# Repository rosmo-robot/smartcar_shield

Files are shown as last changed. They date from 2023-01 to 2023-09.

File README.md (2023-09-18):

# Smartcar shield 2.0







A versatile and easy to use vehicle platform for hobby & Academic projects

## Description
This repository, includes everything necessary to set up a Smartcar 2.0. The 100% open hardware robot down to component level.

The Smartcar, is a vehicular educational platform, which enables the user to develop various robotic applications in an affordable, pedagogic and easy way. It is intended to be accessible for persons with basic programming knowledge and little to no experience of electronics. It additionally supports the needs of more experienced users.

## Smartcar 2.0 (In development)

Licence: CERN-OHL-P

 Features;
 
 * Mounting space for SBC; Beagle AI64, Play, Pi, Jetson Nano, etc 
 * Reference implimentation of Arduino / [Smartcar Library](https://github.com/rosmo-robot/smartcar_shield/blob/master/README.md
 * Reference implimentation of [ROS2/Linorobot2](https://github.com/hippo5329/linorobot2_hardware)
 * Use of 4s LifePO4 or 3s Lipo batteries
 * Dual motor drivers for 4x4 & optional [mecanum drive](https://community.robotshop.com/forum/t/nema-17-mecanum-wheels/55901)
 * [mikroBUS socket](https://www.mikroe.com/mikrobus-shuttle-127mm-2x8-pin-box-header-smd-male)
 * Expanded I2C/ SPI connectors using [Breakout Garden](https://shop.pimoroni.com/collections/breakout-garden), [Qwiic](https://soldered.com/categories/easyc-2/)

### Project Status

 * [Motor board](https://kicanvas.org/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) ordered awaiting testing
   
 * [Pico board](https://kicanvas.org/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) ordered awaiting testing

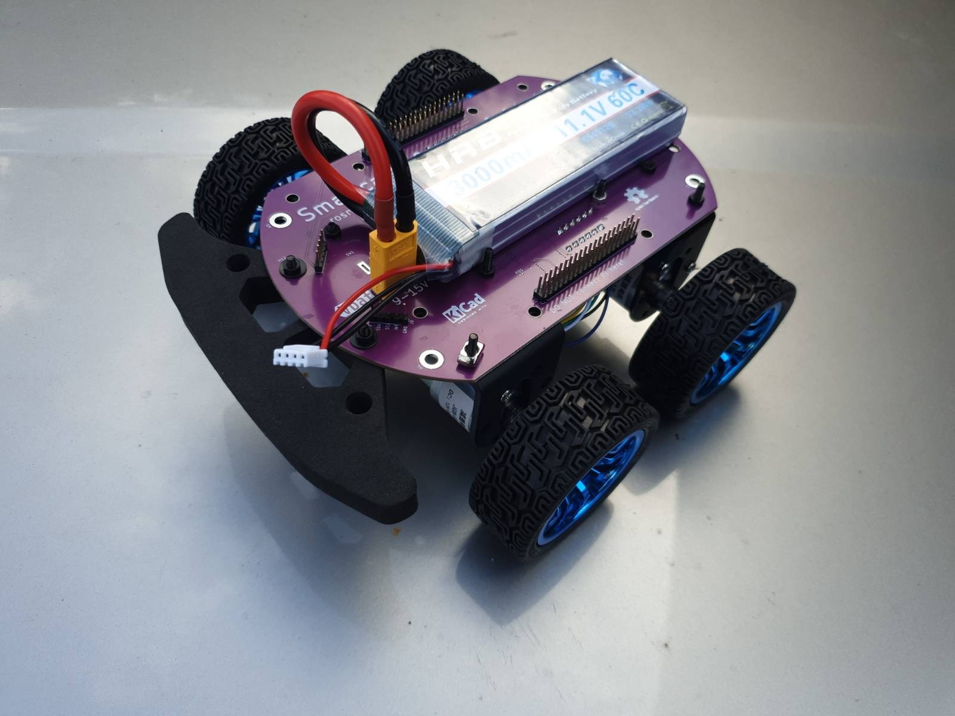
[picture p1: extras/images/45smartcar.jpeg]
Dual driver concept


We hope Smartcar 2.0 interesting to makers, schools and universities. We realise there's no such thing as a universal robot platform, and there are risks in trying to be all things to all people. We however drawn to seeing what's possible with modularity and testing the edges of interoperability.

### Smartcar 2.0 BOM (In development)

* 1 x [Motor board](https://kicanvas.org/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) ordered awaiting testing £11
* 1 X [Pico board](https://kicanvas.org/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) £5
* 4 x [Brushed motors](https://www.aliexpress.com/item/1005004242997257.html) (530rpm @ 12V) £40.50
* 1 x [Olimex Pico](https://www.olimex.com/Products/MicroPython/RP2040-PICO30/open-source-hardware)
* 2 x [40pin 2.54 pitch long male pin headers]()
* 1 x 3S [LifePO4 -recommended](https://www.pulsebattery.com/pages/search-results-page?q=lifePO4%203s) 105 x 33 x 25 or potentially dangerous 3S Lipo battery 135mm*42mm*25mm 304g [~$21 2200Mah](https://www.aliexpress.com/item/1005001419560964.html) > [~$38 4000Mah](https://www.aliexpress.com/item/1005004335619259.html) 135x42x21
* 2 x [Front Bumper](https://www.aliexpress.com/item/1005005024927428.html)

### Optional add ons

* - x [VL45L0x ToF distance sensors](https://shop.pimoroni.com/collections/breakout-garden?tags=Robotics) (optional)
* - X [BNO-85 IMU](https://learn.adafruit.com/adafruit-9-dof-orientation-imu-fusion-breakout-bno085?view=all) (Optional)
* - X [Servo controller](https://www.tindie.com/products/alexchu/zio-16-servo-controller-qwiic/)
* - X [line follower board](https://www.smart-prototyping.com/Zio-Line-Finder-Qwiic-4-Transceivers)
* - X [SPI or I2C Click boards](https://www.mikroe.com/click?interface*=spi,i2c,spi,i2c)
* - X [Aluminum base plate](https://www.aliexpress.com/i/4000265488897.html)
* - Whatever you can bolt to your compute module and get ROS2 to understand, eg cameras, Lidar

### Optional alternative Microcontroller Esp32 S3 (Waveshare)
- Used with [Smartcar Library](https://github.com/platisd/smartcar_shield#software)
- [Linorobot 2 via wifi transport](https://github.com/hippo5329/linorobot2_hardware)
- May also support [Microblocks](https://microblocks.fun/) 

### Single Board Computers (SBC)

We intend to develop some scripts for setting up robotics software on commonly used Single Board Computers which can be added to the basic microcontroller based platform. The OS will be Ubuntu 22.04 LTS. 

The supported hardware may include; 
- [Yuzuki chameleon (OSHW)](https://github.com/YuzukiHD/YuzukiChameleon)
- [Beaglebone Play](https://www.beagleboard.org/boards/beagleplay)
- [Beaglebone Ai-64 (OSHW)](https://beagleboard.org/ai-64) 

Installed software may include

 - Block editor code (TBC)
 - [Pyrobots](https://www.csc.liv.ac.uk/~lad/pyrobots/exercises.html) configuration script
 - [Python app providing a Webui for teleop](https://github.com/DIT112-V19/group-03) Pi GPIO > Micromod.  
 - [Python Robotics](https://github.com/AtsushiSakai/PythonRobotics) Pi GPIO > Micromod
 - [ROS2/Linorobot2](https://github.com/linorobot/linorobot2#linorobot2) USB > Micromod
 - [Rosboard](https://github.com/dheera/rosboard#rosboard) USB > Micromod
 - [Visual circuit](https://github.com/JdeRobot/VisualCircuit#visual-circuit) USB > Micromod
  - [LGPIO](https://ubuntu.com/tutorials/gpio-on-raspberry-pi#1-overview) & [script to set up GPIO](http://4tronix.co.uk/pi2go2/ipd03.py)
 - [Wetty](https://github.com/butlerx/wetty) with [Kaa](http://kaaedit.github.io/)
 - Some demo computer vision code

Linorobot:
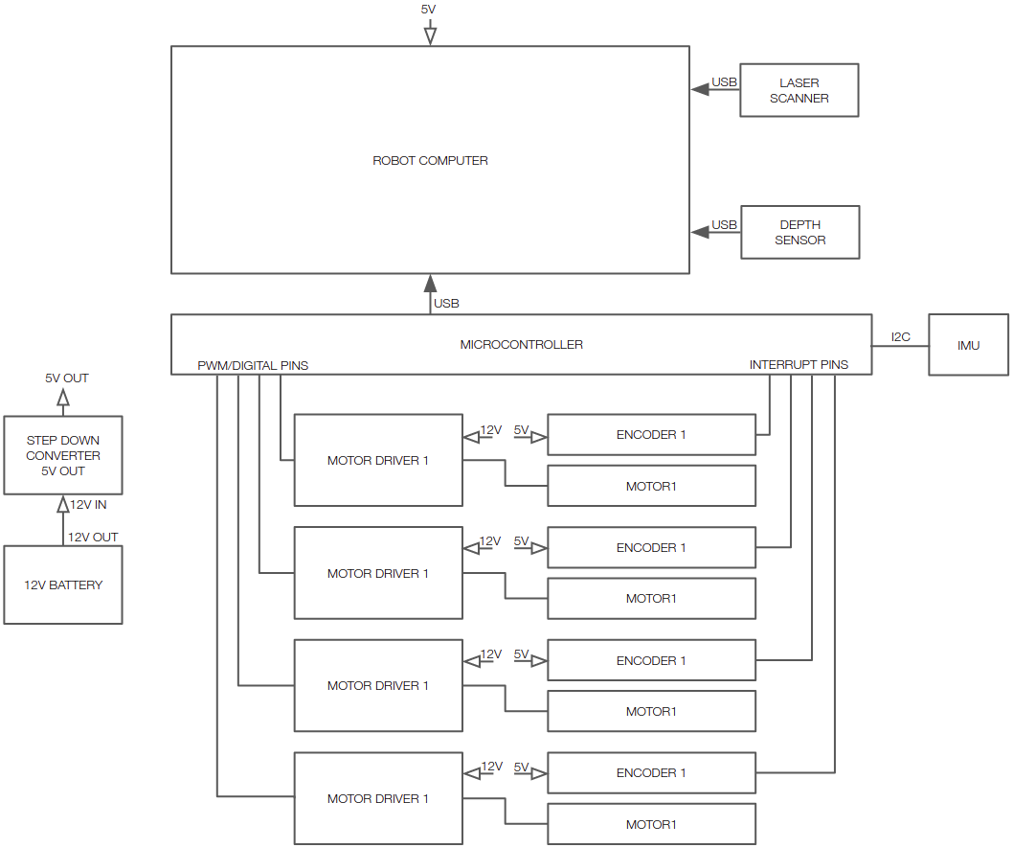
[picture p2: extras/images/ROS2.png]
Linorobot2


### BLDC Version
- Offering an alternate/upgraded BLDC motor board using SimpleFOC, but re-using the 'Modules' board
- Perhaps using [Nema17 BLDC](https://www.omc-stepperonline.com/brushless-dc-motor?mfp=184-frame-size-mm[Nema%2017%20(42%20x%2042)]) to give access to [brackets](https://www.omc-stepperonline.com/nema-17-bracket-for-stepper-motor-and-geared-stepper-motor-alloy-steel-bracket-st-m1) & [gearboxes](https://www.aliexpress.com/premium/nema-17-gearbox.html)

### License
MIT & CERN-OHL-P for Smartcar 2.0 hardware

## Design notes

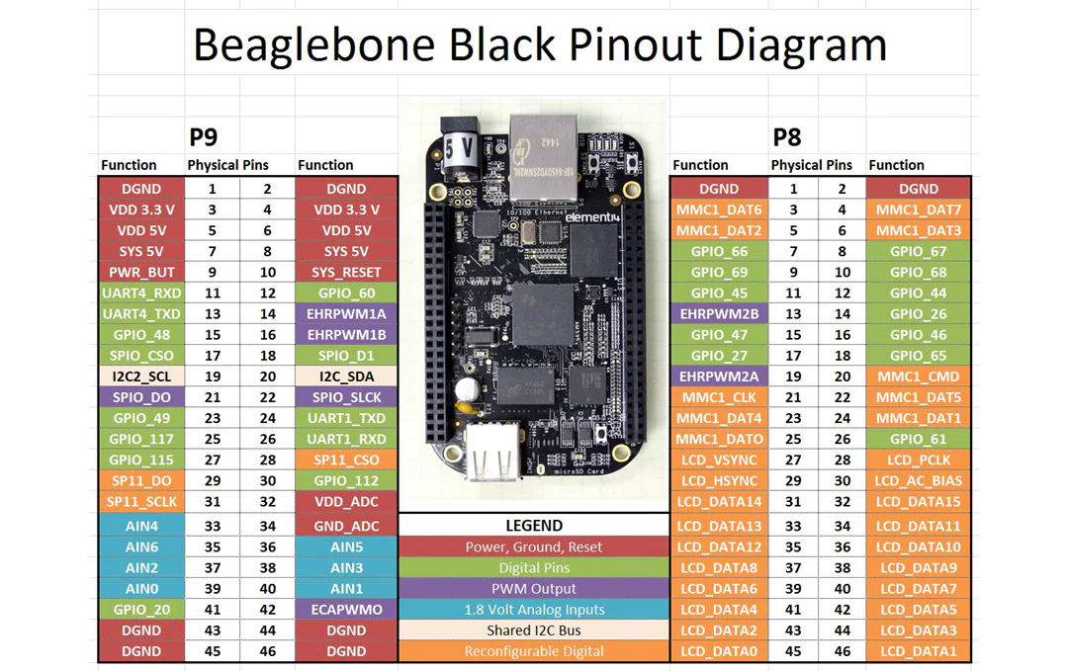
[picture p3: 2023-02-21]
extras/kicad/V2/Control/BeagleBone_Black_Pinout.webp

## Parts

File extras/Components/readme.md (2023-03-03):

Micromod

[RP2040 pin table](https://learn.sparkfun.com/tutorials/micromod-rp2040-processor-board-hookup-guide#hardware-overview)

[Teensy pin table](https://learn.sparkfun.com/tutorials/micromod-teensy-processor-hookup-guide/hardware-overview)

[ESP32 pin table](https://learn.sparkfun.com/tutorials/micromod-esp32-processor-board-hookup-guide/hardware-overview)

[SNO pin table](https://cdn.sparkfun.com/r/600-600/assets/learn_tutorials/2/2/8/7/AloriumSnoM2PinMap.png)

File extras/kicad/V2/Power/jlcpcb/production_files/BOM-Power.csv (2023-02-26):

Comment | Designator | Footprint | LCSC
INA219AxD | U5 | SOIC-8_3.9x4.9mm_P1.27mm | C138706
100n | C1,C11,C12,C14,C2,C21,C23,C25,C34,C4,C5,C8 | C_0603_1608Metric | C14663
1n5 | C16,C26 | C_0603_1608Metric_Pad1.08x0.95mm_HandSolder | C1595
D | D1,D2 | D_SMA | C22452
150k | R11 | R_0603_1608Metric_Pad0.98x0.95mm_HandSolder | C22807
15k | R10 | R_0603_1608Metric_Pad0.98x0.95mm_HandSolder | C22809
3k3 | R6 | R_0603_1608Metric_Pad0.98x0.95mm_HandSolder | C22978
0.1 | R12,R13,R2,R7,R9 | R_1206_3216Metric_Pad1.30x1.75mm_HandSolder | C25334
10k | R1,R3,R4,R8 | R_0603_1608Metric | C25804
15u | L1,L2 | Inductor SMD,11.6x10.1x4mm | C3002687
SS01-BBIWA-RA20-R | SW1 | SW-TH_SS01-BBIWA-RA20-R | C309065
2k2 | R5 | R_0603_1608Metric_Pad0.98x0.95mm_HandSolder | C4190
22u | C10,C3,C35,C36,C37,C38,C39,C6,C7,C9 | C_0805_2012Metric | C45783
TB6612FNG | U1,U2 | SSOP-24_5.3x8.2mm_P0.65mm | C88224
47u | C13,C15,C17,C18,C19,C20,C22,C24,C27,C28,C29,C30,C31,C32,C33 | C_1206_3216Metric | C96123
TPS5430DDAR | U3,U4 | SOIC-8-1EP_3.9x4.9mm_P1.27mm_EP2.29x3mm_ThermalVias | C9864
XT60PW-M | J1 | CONN-TH_XT60PW-M | C98732
Conn_01x05 | J8 | PinHeader_1x05_P2.54mm_Vertical
left | J6 | PinHeader_2x20_P2.54mm_Vertical
Conn_01x05 | J9 | PinHeader_1x05_P2.54mm_Vertical
right | J7 | PinHeader_2x20_P2.54mm_Vertical
Polyfuse | F1 | Fuse_2920_7451Metric_Pad2.10x5.45mm_HandSolder
Screw_Terminal_01x06 | J3 | TerminalBlock_4Ucon_1x06_P3.50mm_Horizontal
Screw_Terminal_01x06 | J5 | TerminalBlock_4Ucon_1x06_P3.50mm_Horizontal
Screw_Terminal_01x06 | J4 | TerminalBlock_4Ucon_1x06_P3.50mm_Horizontal
Screw_Terminal_01x06 | J2 | TerminalBlock_4Ucon_1x06_P3.50mm_Horizontal

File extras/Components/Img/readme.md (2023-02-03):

Photos of bits it would be nice to get working on [Smartcar 2.0](https://github.com/rosmo-robot/smartcar_shield#smartcar-20-in-development)

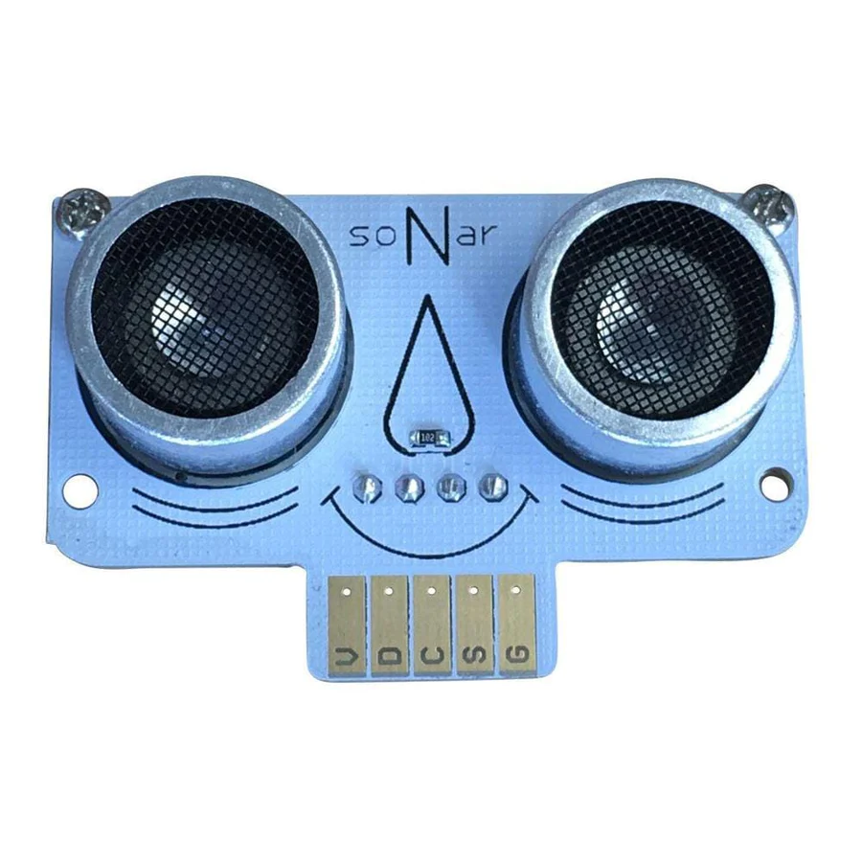
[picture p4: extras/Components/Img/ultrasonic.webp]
 

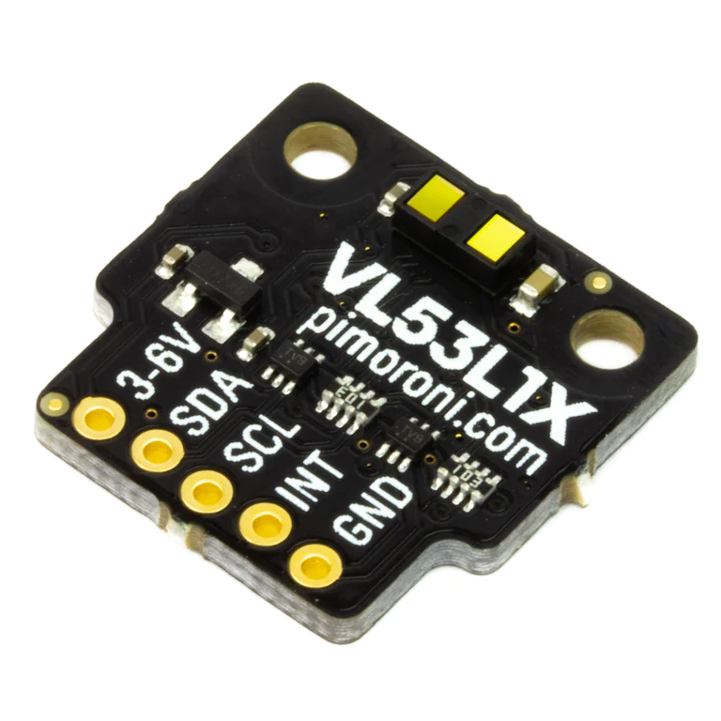
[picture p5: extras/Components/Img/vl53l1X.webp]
 

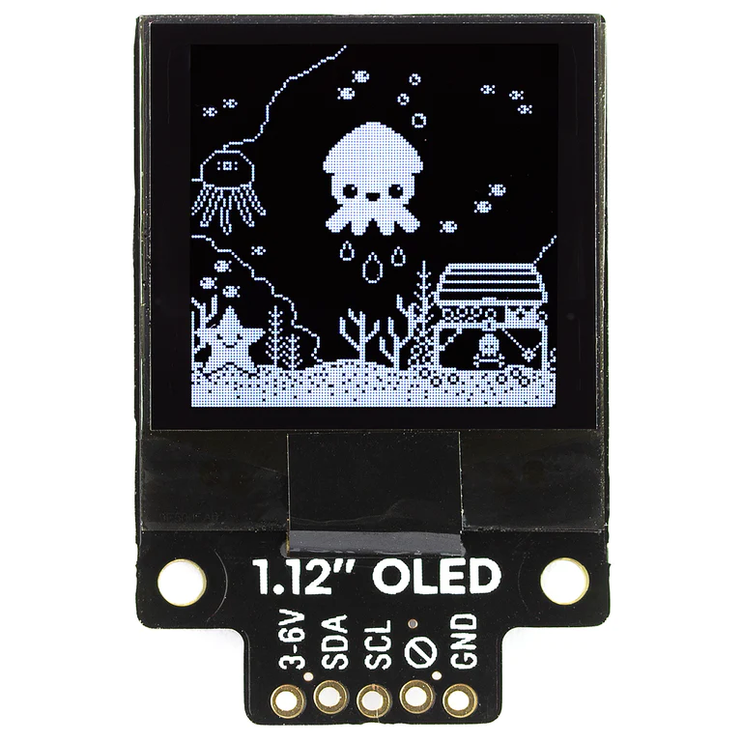
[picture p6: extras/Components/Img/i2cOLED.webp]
 

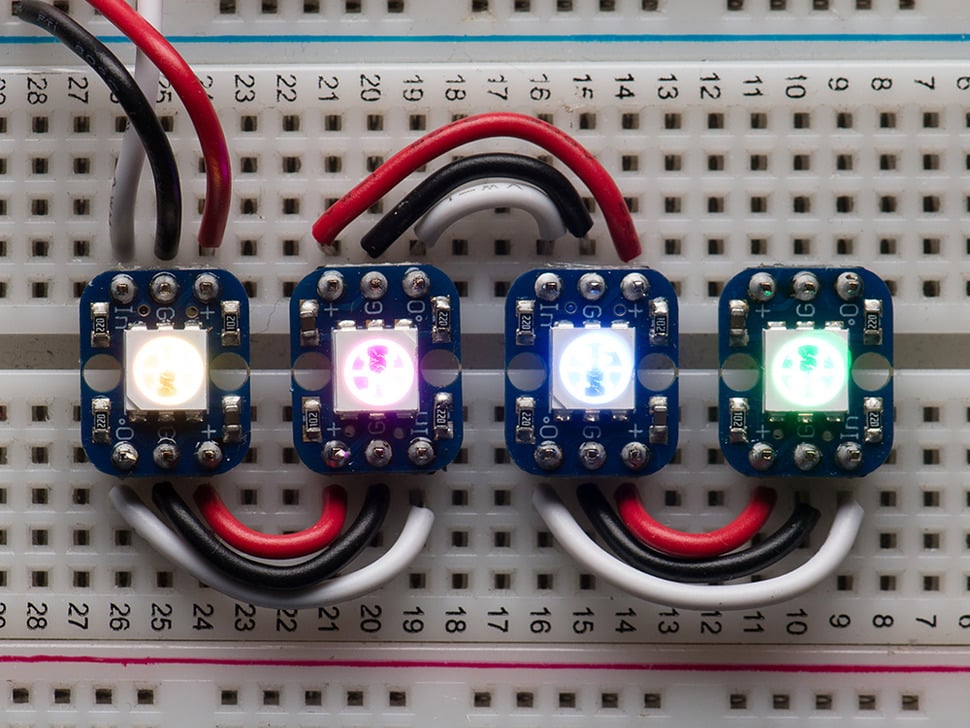
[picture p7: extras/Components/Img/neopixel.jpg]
 

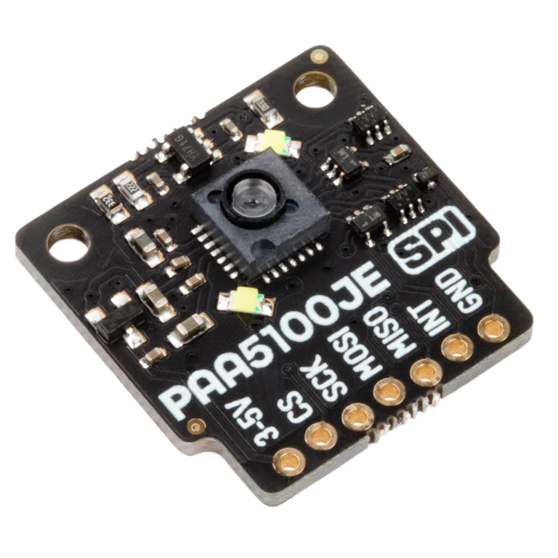
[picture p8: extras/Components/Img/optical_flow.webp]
 

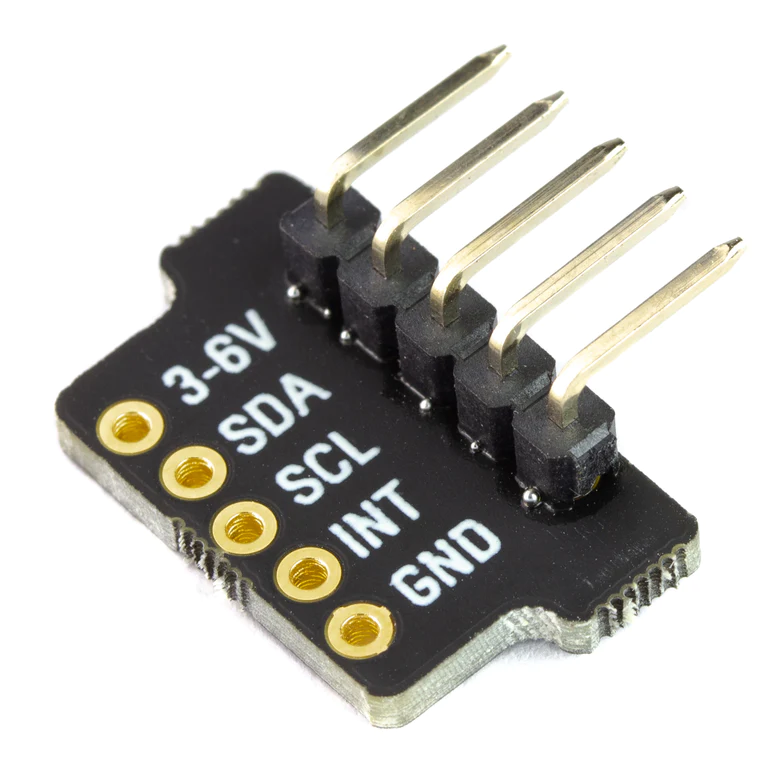
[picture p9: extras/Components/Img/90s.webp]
 

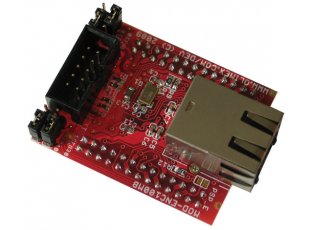
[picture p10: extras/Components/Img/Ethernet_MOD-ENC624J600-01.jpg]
 

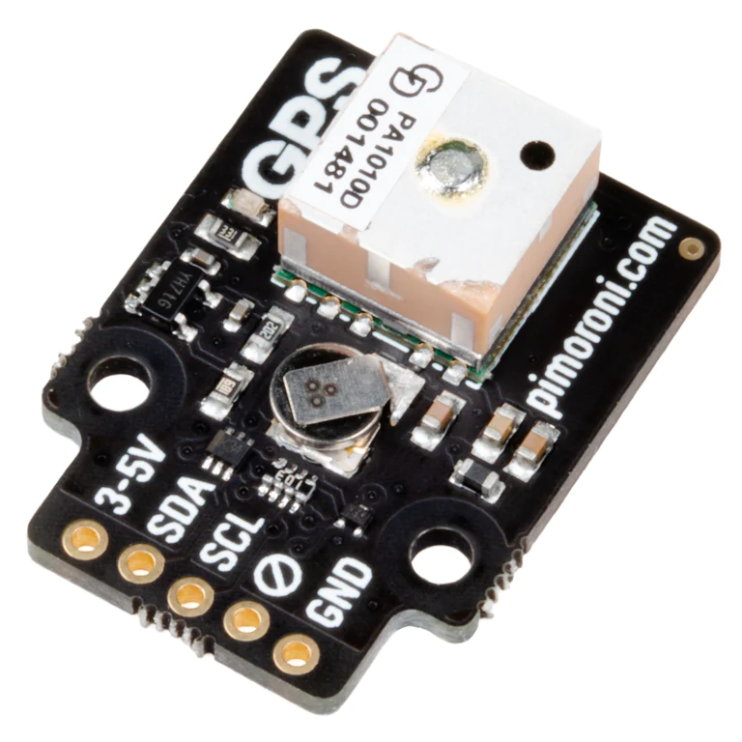
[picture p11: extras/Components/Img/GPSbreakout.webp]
 

 

 

 

 

 

Back to [Smartcar 2.0](https://github.com/rosmo-robot/smartcar_shield#smartcar-20-in-development)

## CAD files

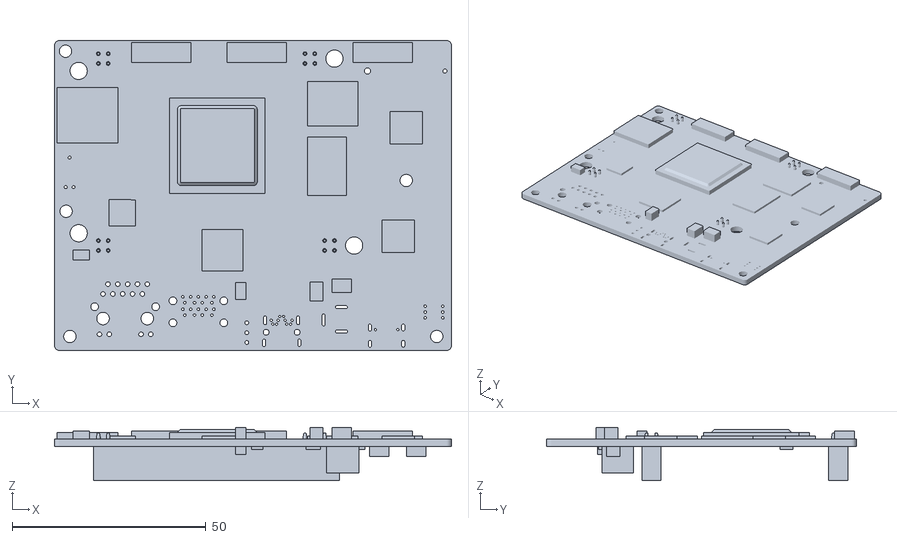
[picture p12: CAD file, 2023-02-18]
extras/Components/BeagleBone_AI-64_Rev_B1_3D_220826.dxf
102.5 x 80.0 x 13.8

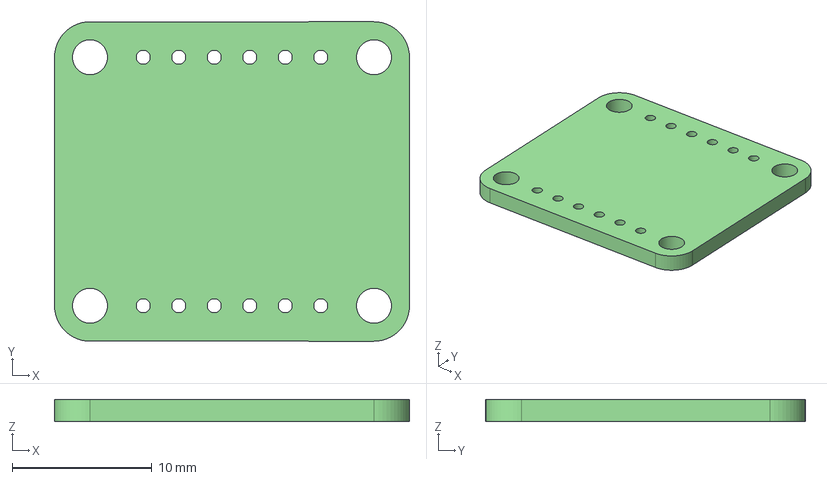
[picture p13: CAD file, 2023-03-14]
extras/kicad/V2/Control/3D/BNO85.step
25.4 x 22.9 x 1.60 mm

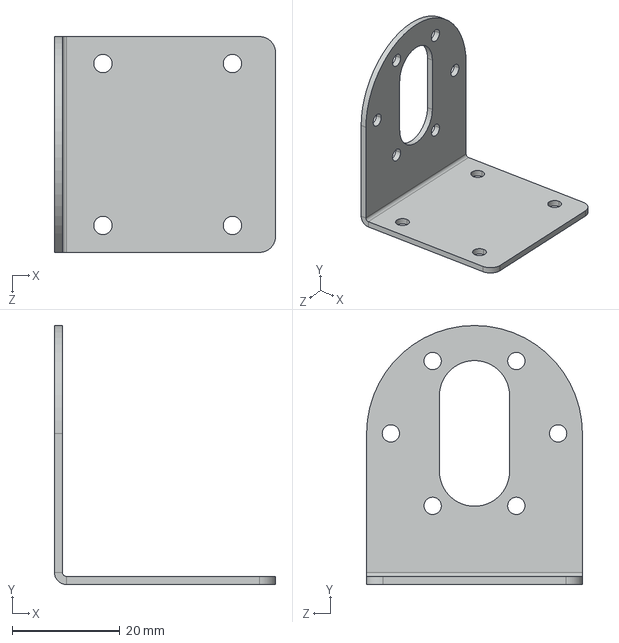
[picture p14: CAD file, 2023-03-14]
extras/kicad/V2/Control/3D/37 mm DC Geared Motor Mounting Bracket.STEP
41.0 x 48.0 x 40.0 mm

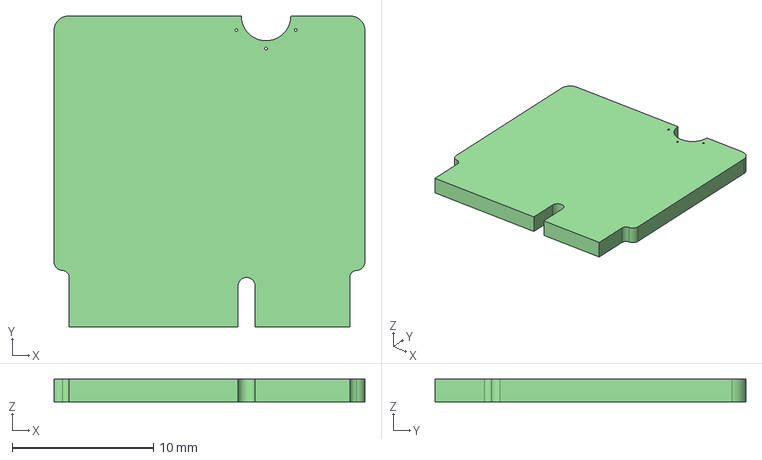
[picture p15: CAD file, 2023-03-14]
extras/kicad/V2/Control/3D/MicroMod_Processor_Board.step
22.0 x 22.0 x 1.60 mm

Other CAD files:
extras/Components/TB3_Waffle_Plate-IPL-01.dwg

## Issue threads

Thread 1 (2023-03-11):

Dual motor control in Smartcar lib

samuk, 2023-03-11:
## Description

The existing Smart car Lib is designed for a single-motor driver: https://github.com/rosmo-robot/smartcar_shield/tree/master/src/motor This robot has two motor drivers.

See also https://github.com/adityakamath/akros2_firmware/tree/akros2_galactic/src/motor for dual motor implementation using micro_ros_arduino

## Definition of Done

It is possible to control two TB6612FNG using the code in this repo

platisd, 2023-03-11:
How many different motors are there in total?
Is it two on each driver?

platisd, 2023-03-11:
Anyway, unless I have misunderstood you, the linked pull request should solve this issue and it makes sense to be supported by `smartcar_lib`.

samuk, 2023-03-11:
Yes, that's correct two motors per driver. Thanks for the pull! Will take a look now

platisd, 2023-03-11:
The mecanum use case would fall under a different/new way of "steering". But as long as we have all the other building blocks together it shouldn't be an issue to fit right in along with the rest of the library.

I could consider supporting the mecanum as a way of steering the car on the upstream library as long as it's not overly complex or disruptive.

samuk, 2023-03-11:
Great stuff. Maybe there's something in how the [Linorobot2 codebase handles switching](https://github.com/linorobot/linorobot2_hardware/blob/galactic/config/lino_base_config.h#L20) that's useful to emulate/copy?

adityakamath, 2023-03-11:
Hey @platisd I had a look at the PR and it looks good to me! I think with this, adding mecanum control should be quite straightforward IMO, especially in the open loop case.

For closed loop, with an encoder on each wheel/motor, I'm not sure how disruptive the changes would be. Are 4 encoders supported right now?

platisd, 2023-03-11:
Thinking of it more carefully, the mecanum case may actually not be able to satisfy the [Control interface](https://github.com/platisd/smartcar_shield/blob/master/src/control/Control.hpp).
If I've understood it right with mecanum you can move sideways etc, which is not modeled in the current design of the library.
So I'm taking back what I said before. Integrating it with the rest is not trivial at all as it's too different compared to the current ways of steering.

To put it simply, you can't fully control a mecanum car with `setSpeed` and `setAngle` as you do with a conventional car.

adityakamath, 2023-03-11:
Can I propose updating the interface by splitting `setSpeed` into `setXSpeed` and `setYSpeed`? It would still work with the existing drive configs (by setting Y speed to 0). Then, controlling a mecanum car should be possible.

platisd, 2023-03-12:
> Can I propose updating the interface by splitting `setSpeed` into `setXSpeed` and `setYSpeed`? It would still work with the existing drive configs (by setting Y speed to 0). Then, controlling a mecanum car should be possible.

@adityakamath
To begin with, updating an interface and adding some functions that don't make sense all its users (i.e. the "conventional" cars) is generally considered a bad idea. If we are adding `setXSpeed` and `setYSpeed` methods then these definitely belong in a different interface. That's something to consider in the future though, look at point (3) later on.

But you made me start thinking more. :sweat_smile: :bulb:

The `Control` interface also exposes the [`overrideMotorSpeed`](https://github.com/platisd/smartcar_shield/blob/master/src/control/Control.hpp#L62) function which allows for "advanced" users to have more accurate control over the output towards the motors. I can consider renaming the function to something that makes sense for all the use-cases. We can be creative with the name, so I don't think that will be an issue.
It's also good the existing `Car` classes don't use the particular method other than relaying the arguments passed to it to the `Control` interface. It won't disrupt anything that currently works in other words.

To sum up my thoughts and conclude:
1. Could we have a mecanum car, driven like a conventional car (and get all the existing functionality for "free") if we sacrifice the side-ways moving functionality and set one of the axis' speed to `0`? From the user's perspective if would look something like:
```cpp
MecanumControl control{motor1, motor2, motor3, motor4}; // There are 4 motors right?
SimpleCar car{control};

car.setSpeed(50); // Move only towards one axis "forward"
// Turn like a conventional car/tank
car.setAngle(90); // No speed on "one side of the car", 50% speed on the other side
```
2. Then if the user wants to move side ways:
```cpp
// Consider we may rename `overrideMotorSpeed` to something better
car.overrideMotorSpeed(50, 100); // 50% x-speed, 100% y-speed
```
3. In the long run,there should probably be a set of `MecanumCar` classes, i.e. `SimpleMecanumCar`, `DistanceMecanumCar`, `SmartMecanumCar` which should (not?) have any `setSpeed` and `setAngle` methods. But let's keep that in the back of our heads and not discuss further until we must.

@samuk @adityakamath Do you think using a mecanum car as described in (1) and (2) is acceptable for the users?

adityakamath, 2023-03-12:
Not sure how acceptable it will be for users, but it definitely is a start for providing mecanum support.

@samuk I think the goal should be to first provide micro ROS support to the existing configurations, and eventually after some brainstorming, we can add the mecanum support as well.

samuk, 2023-03-12:
Great, that sounds like a good approach. Getting the skid steer working on the hardware is likely to be a bit of work in itself.

So I think the proposed pull would resolve this ticket. Thanks, @platisd

Closed 2023-03-13.

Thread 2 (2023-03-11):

BNO085 IMU support

samuk, 2023-03-11:
## Description

The existing code supports GY-50 IMU

## Definition of Done

It is possible to use BNO085 IMU with this lib

platisd, 2023-03-11:
If someone really wanted to integrate this, it'd be relatively simple considering that Adafruit has done a good job on creating a [very easy library](https://github.com/adafruit/Adafruit_BNO08x_RVC/blob/master/examples/uart_rvc/uart_rvc.ino).

If you really want, I can create an simple wrapper for it, which would make it compatible with the rest of the Smartcar library, but I will **not** be including it in the "upstream" Smartcar library for reasons we've previously discussed if  I am not mistaken.

I don't have the means to test it and I will not be creating unit tests for it, but it looks simple enough to minimize the chances of issues.

samuk, 2023-03-11:
A wrapper would be great, thanks I'll order one and can test it.

immortal-sniper1, 2023-03-13:
@samuk  who is @platisd ?

samuk, 2023-03-13:
[@platisd](https://github.com/platisd) is the boss :)

He developed the original [hardware platform]( https://platis.solutions/blog/2020/02/16/smartcar-gets-an-esp32-upgrade/), he also wrote and[ maintains the Smartcar Shield library](https://github.com/platisd/smartcar_shield#software)

immortal-sniper1, 2023-03-14:
ok

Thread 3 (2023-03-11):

Support LIS3DH

samuk, 2023-03-11:
## Description
https://github.com/rosmo-robot/smartcar_shield/tree/master/src/sensors/heading
Add LIS3DH support to the lib

## Definition of Done

Sensor data from LIS3DH is available

platisd, 2023-03-11:
[This one](https://github.com/adafruit/Adafruit_LIS3DH/blob/master/examples/acceldemo/acceldemo.ino) seems more tricky as the sensor's output is in `m/s^2` and not in degrees.
This means that some maths are needed and I am not personally interested in trying to figure that part out. Also, if I am not mistake this is only an accelerometer meaning that it is **not** good or suitable for determining the heading of a vehicle.

samuk, 2023-03-12:
Hmm, thanks. We included this  ~$1 component without a great deal of research. It may be better to replace it with a ~$3 L3G4200D or MPU6050. I'll go and investigate a hardware change.

Closed 2023-03-12.

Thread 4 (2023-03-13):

Evaluate MPU6500 as on-board IMU

samuk, 2023-03-13:
## Description

Evaluate this as the 'onboard' budget IMU: https://www.lcsc.com/search?q=mpu6500

This lib looks most promising: https://github.com/wollewald/MPU9250_WE

This is the [MPU6500 example](https://github.com/wollewald/MPU9250_WE/blob/main/examples/MPU6500_all_data/MPU6500_all_data.ino) from that lib

## Definition of Done

Comments that the hardware/lib looks worth evaluating on real hardware.

adityakamath, 2023-03-18:
I'll check it out. For starters, the 6500 seems to be related to the MPU6050 and MPU9250. I've used them before and there are multiple libraries to access data from them. Data from 6050 and 9250 is on the noisier side compared to BNO055 or similar IMUs, but decent enough given the price.

samuk, 2023-03-18:
Great thanks, if people find the limitations of it they could always upgrade to the BNO085

adityakamath, 2023-03-20:
Had a look at the sensor itself, looks good. From the documentation (of the library), MPU6500 seems to be a MPU9250 but without the magnetometer. I assume the library works (given the number of stars and watchers). If not, there are quite a lot of libraries around for the MPU9250/6500

IMO should be sufficient as an on-board IMU

samuk, 2023-03-20:
Great, thanks. We'll add it to the board

Closed 2023-03-20.

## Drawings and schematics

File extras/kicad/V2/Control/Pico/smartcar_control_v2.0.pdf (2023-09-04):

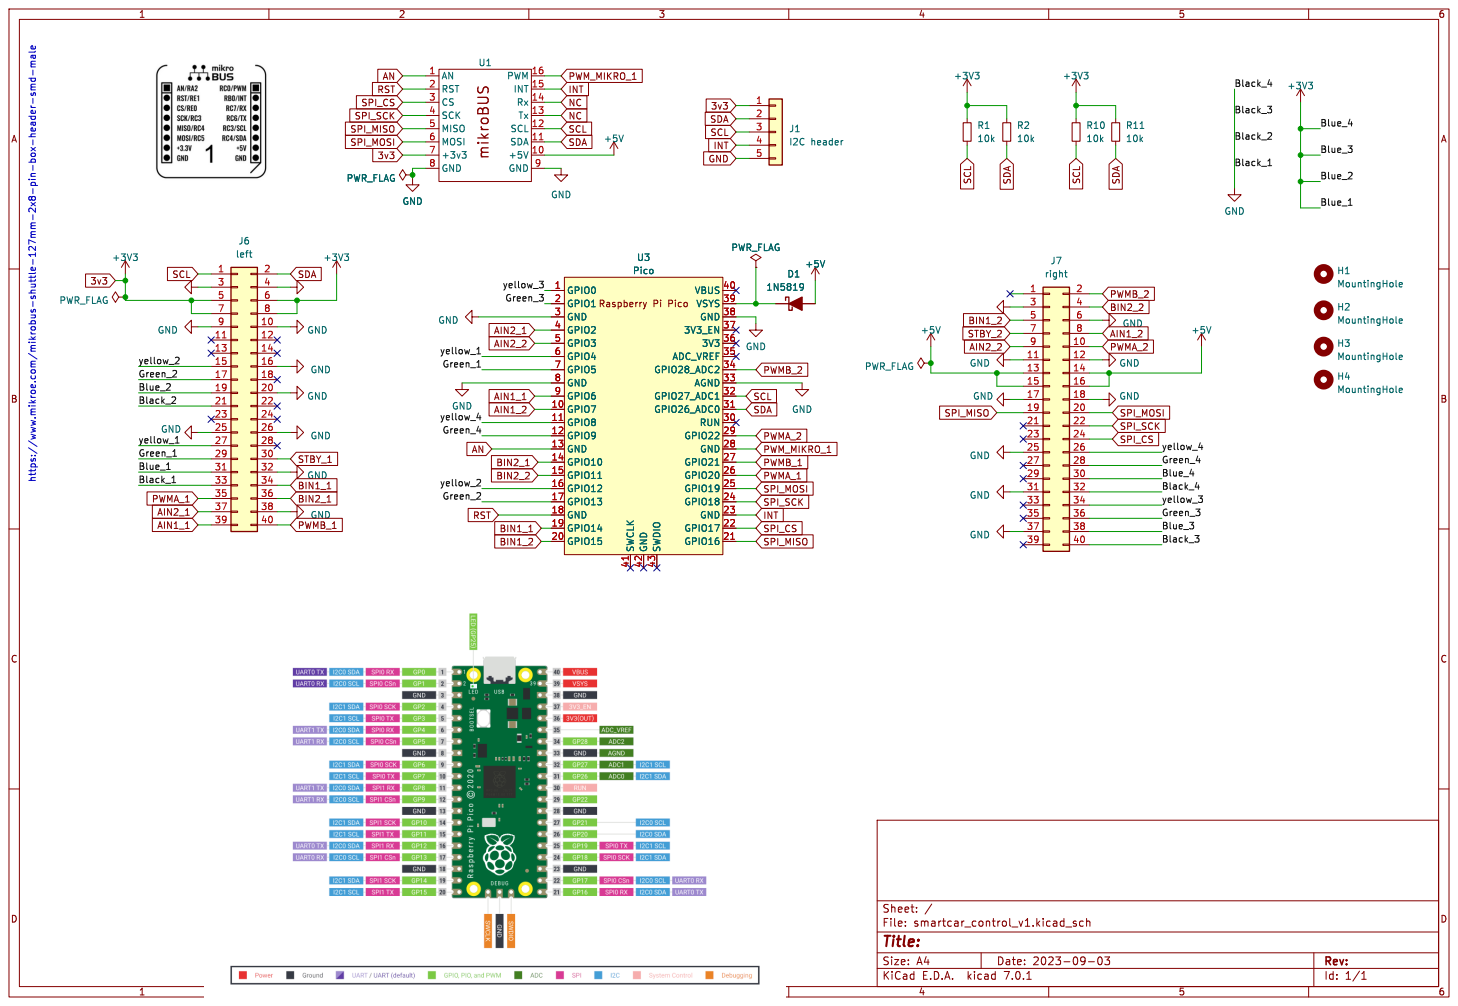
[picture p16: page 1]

H2 MountingHole GND GND GNDGND

Id: 1/1 Title: File: smartcar_control_v1.kicad_sch Sheet: /

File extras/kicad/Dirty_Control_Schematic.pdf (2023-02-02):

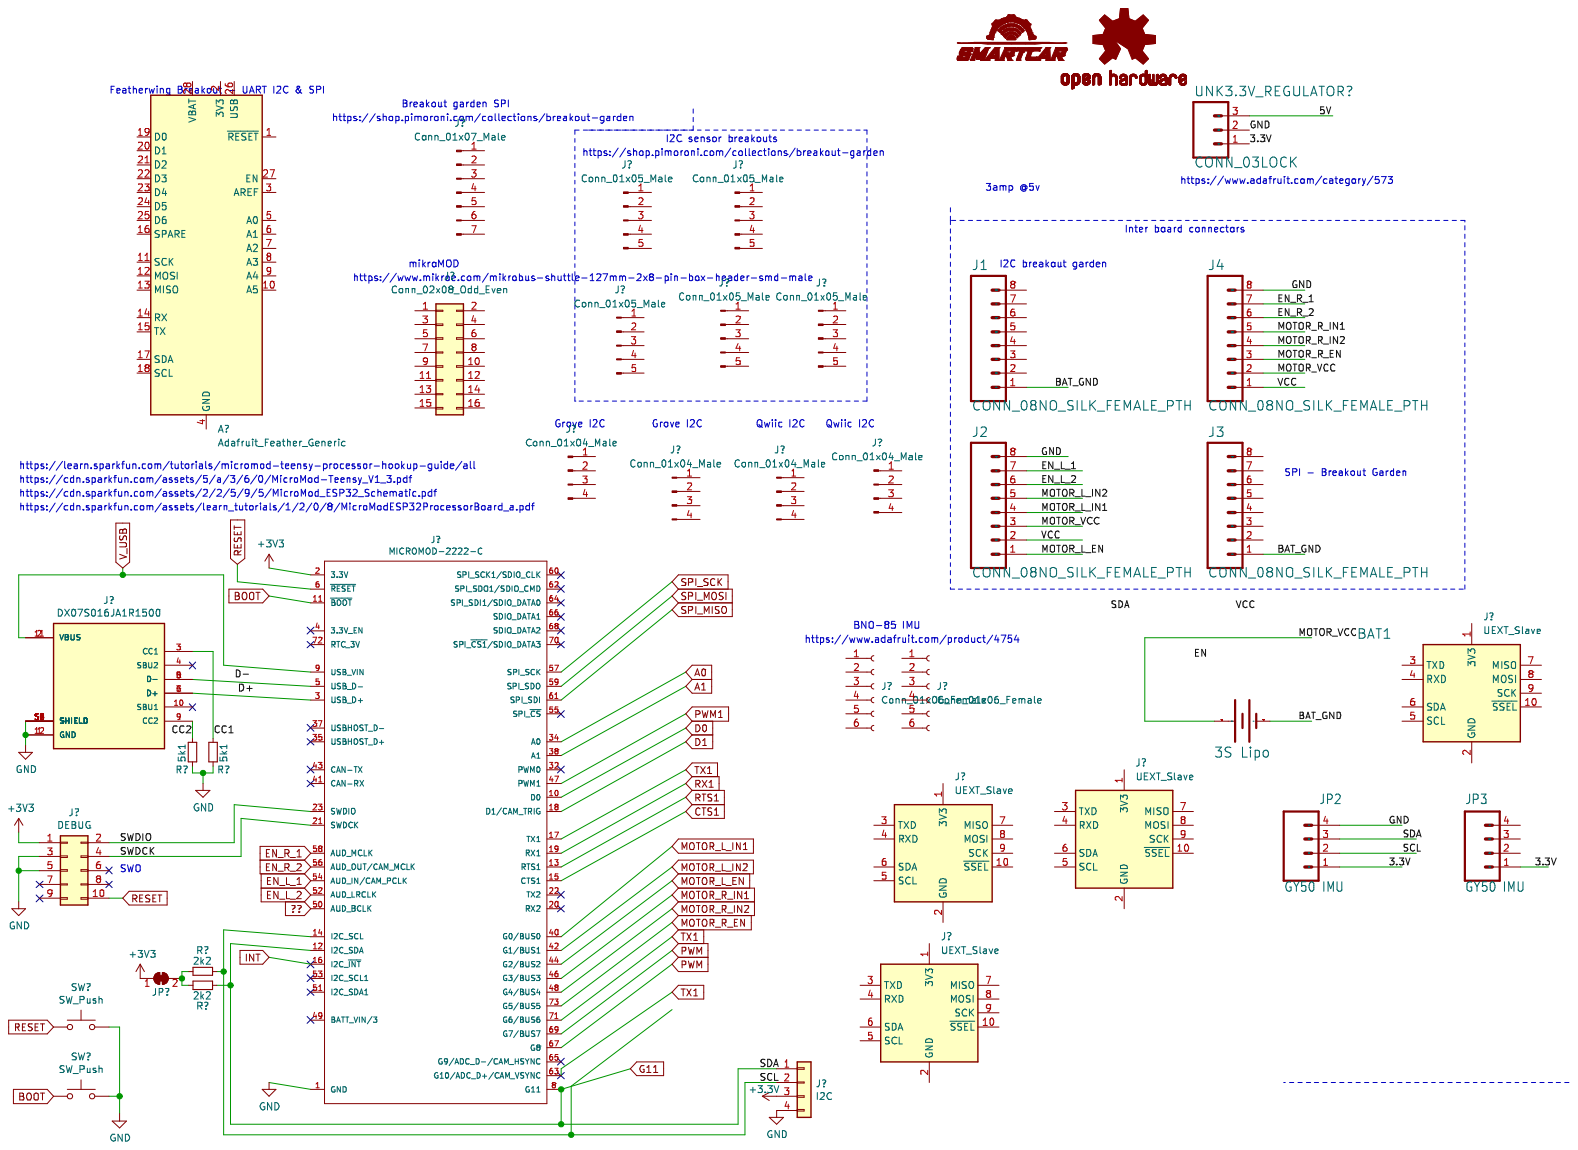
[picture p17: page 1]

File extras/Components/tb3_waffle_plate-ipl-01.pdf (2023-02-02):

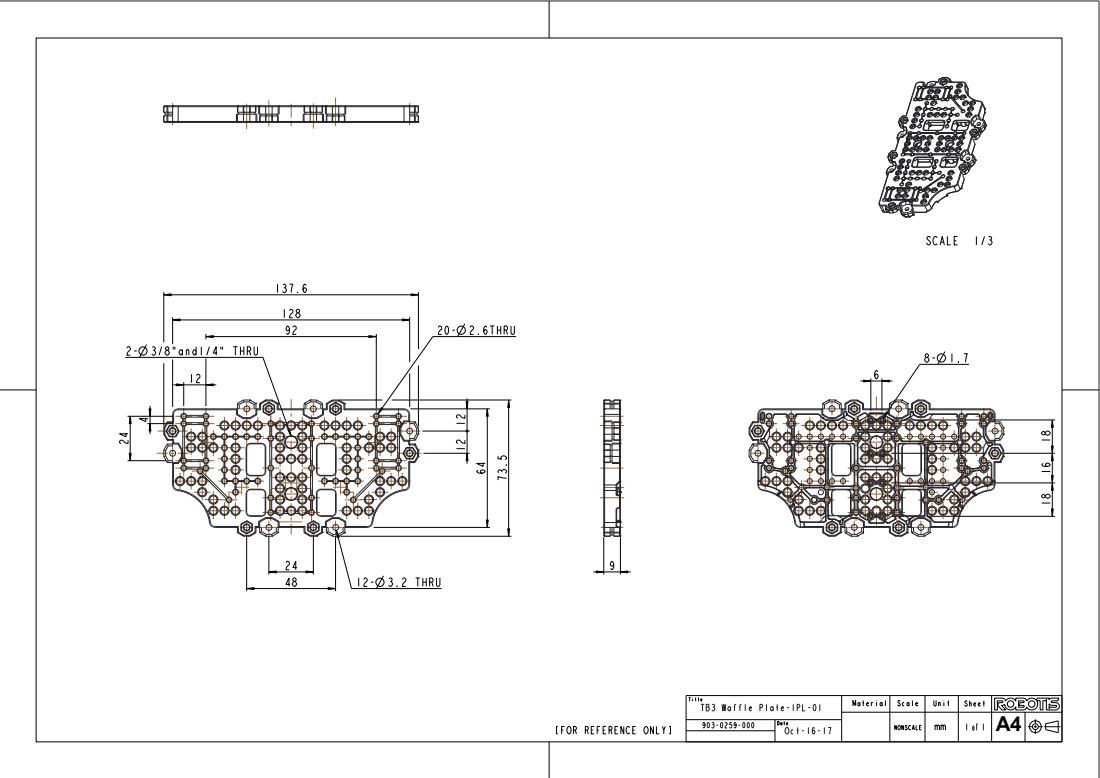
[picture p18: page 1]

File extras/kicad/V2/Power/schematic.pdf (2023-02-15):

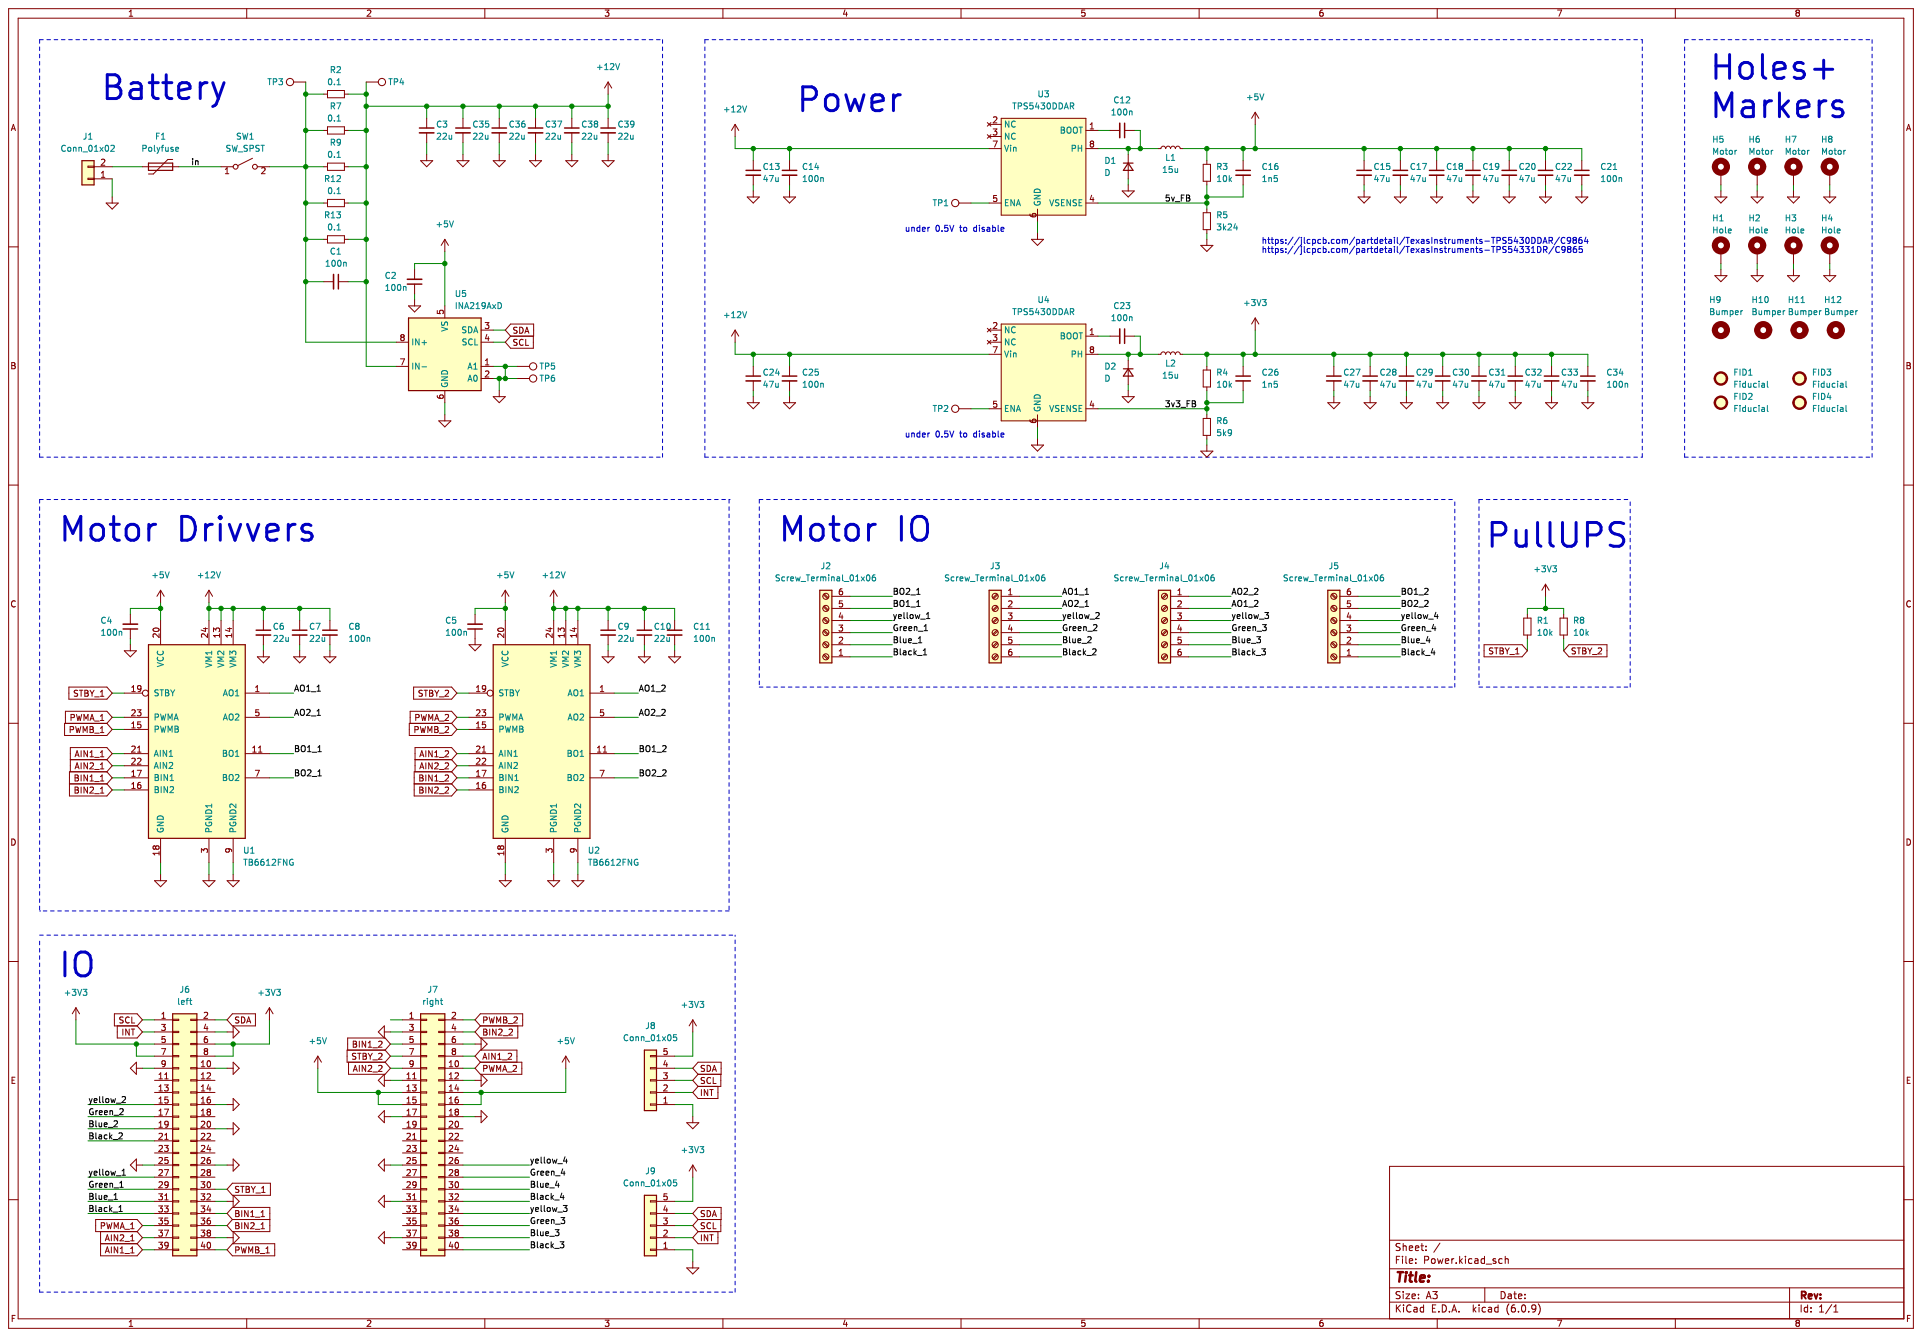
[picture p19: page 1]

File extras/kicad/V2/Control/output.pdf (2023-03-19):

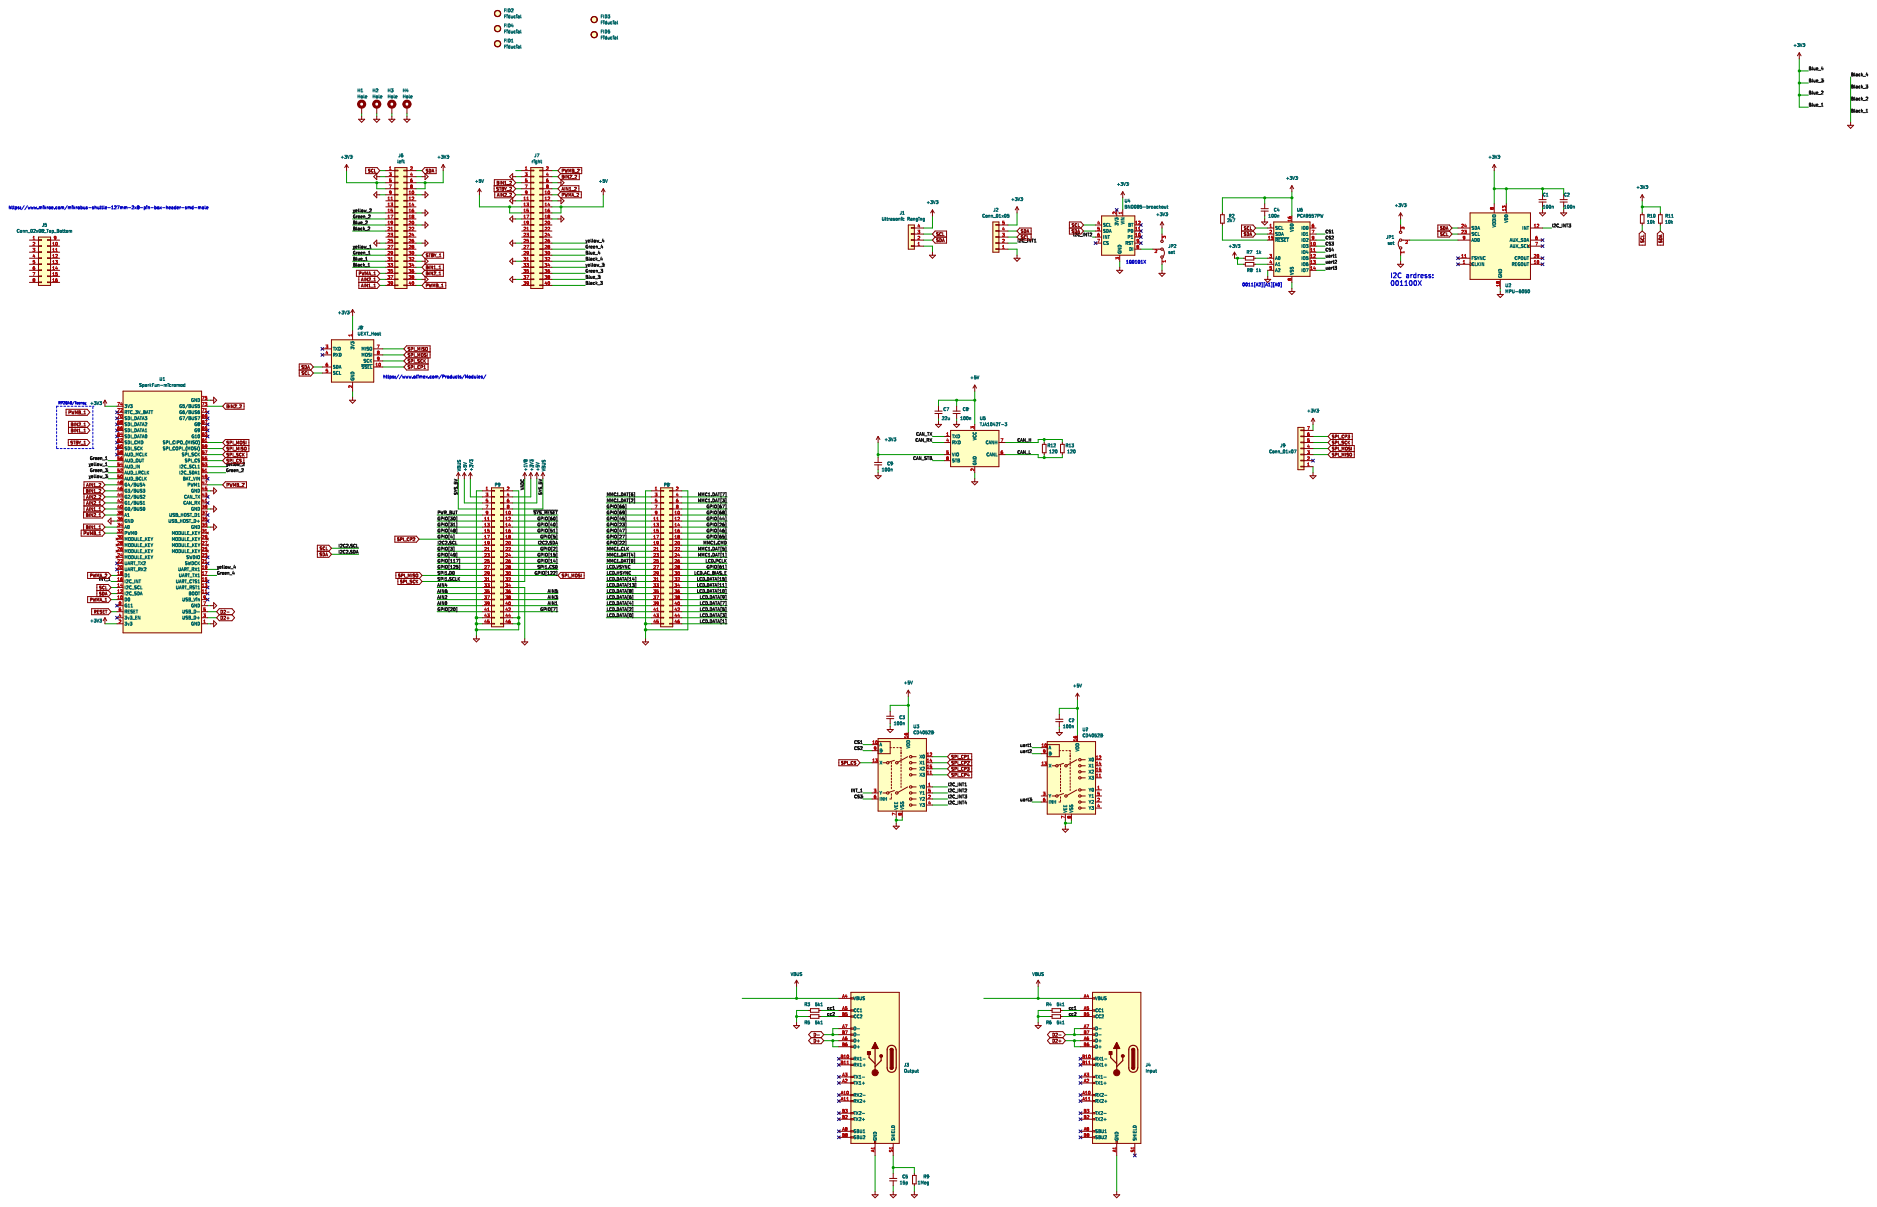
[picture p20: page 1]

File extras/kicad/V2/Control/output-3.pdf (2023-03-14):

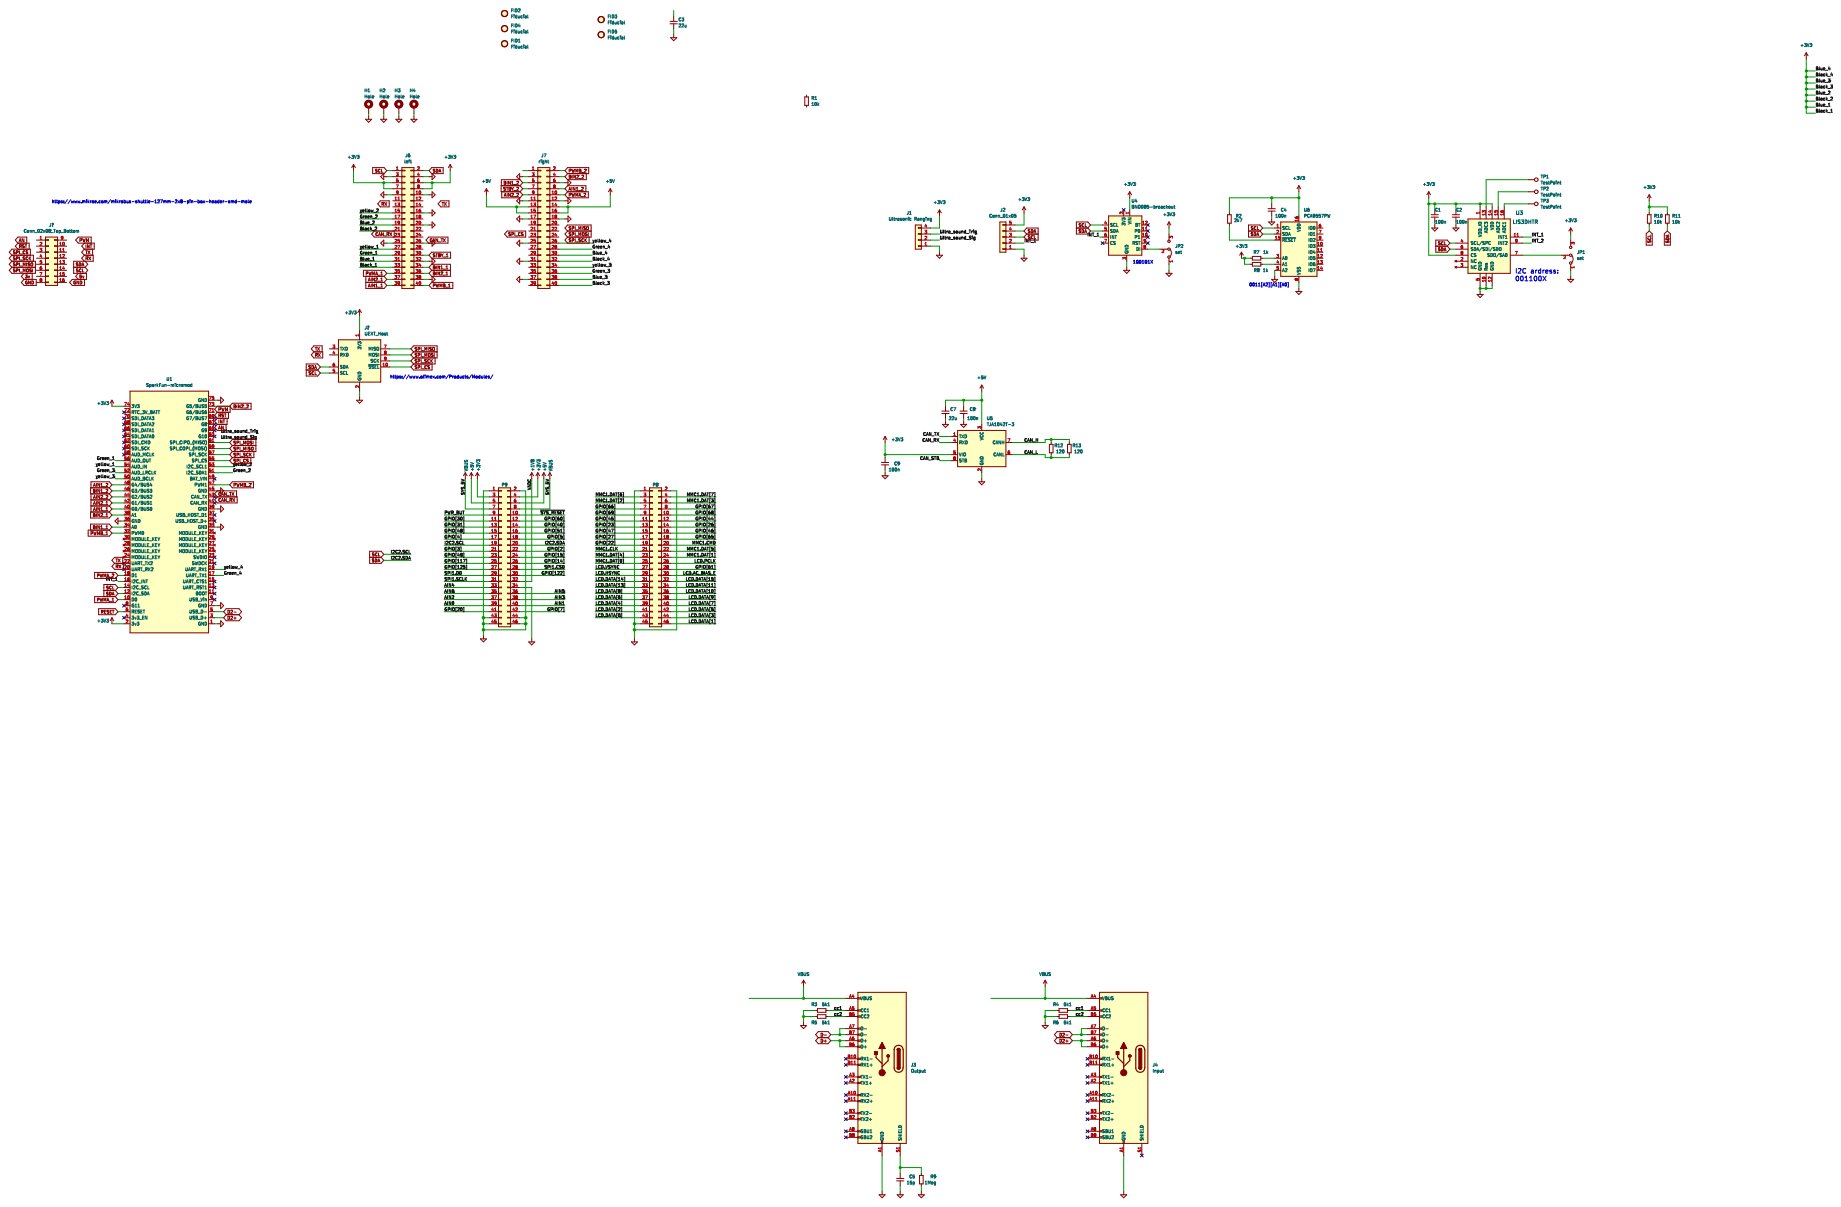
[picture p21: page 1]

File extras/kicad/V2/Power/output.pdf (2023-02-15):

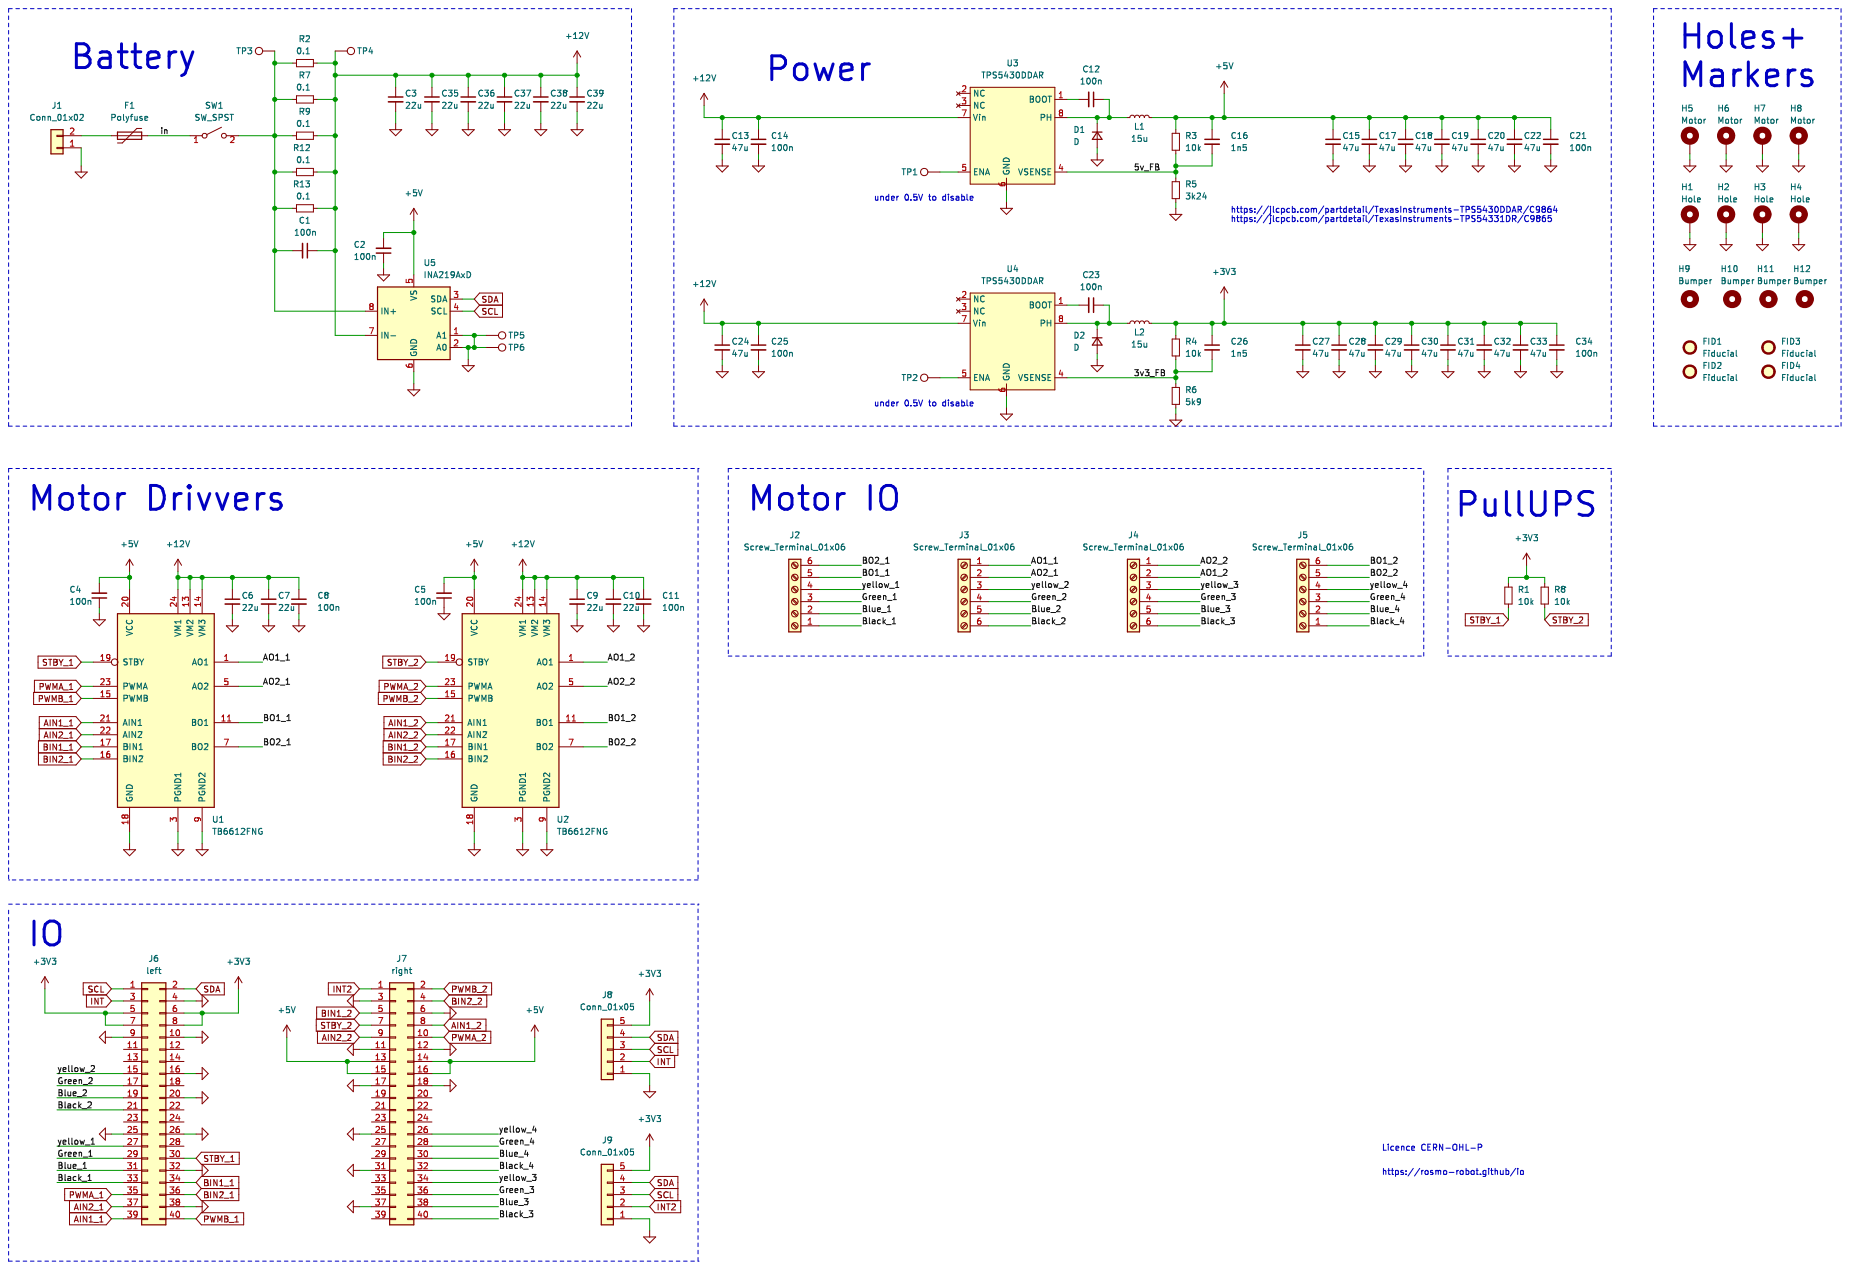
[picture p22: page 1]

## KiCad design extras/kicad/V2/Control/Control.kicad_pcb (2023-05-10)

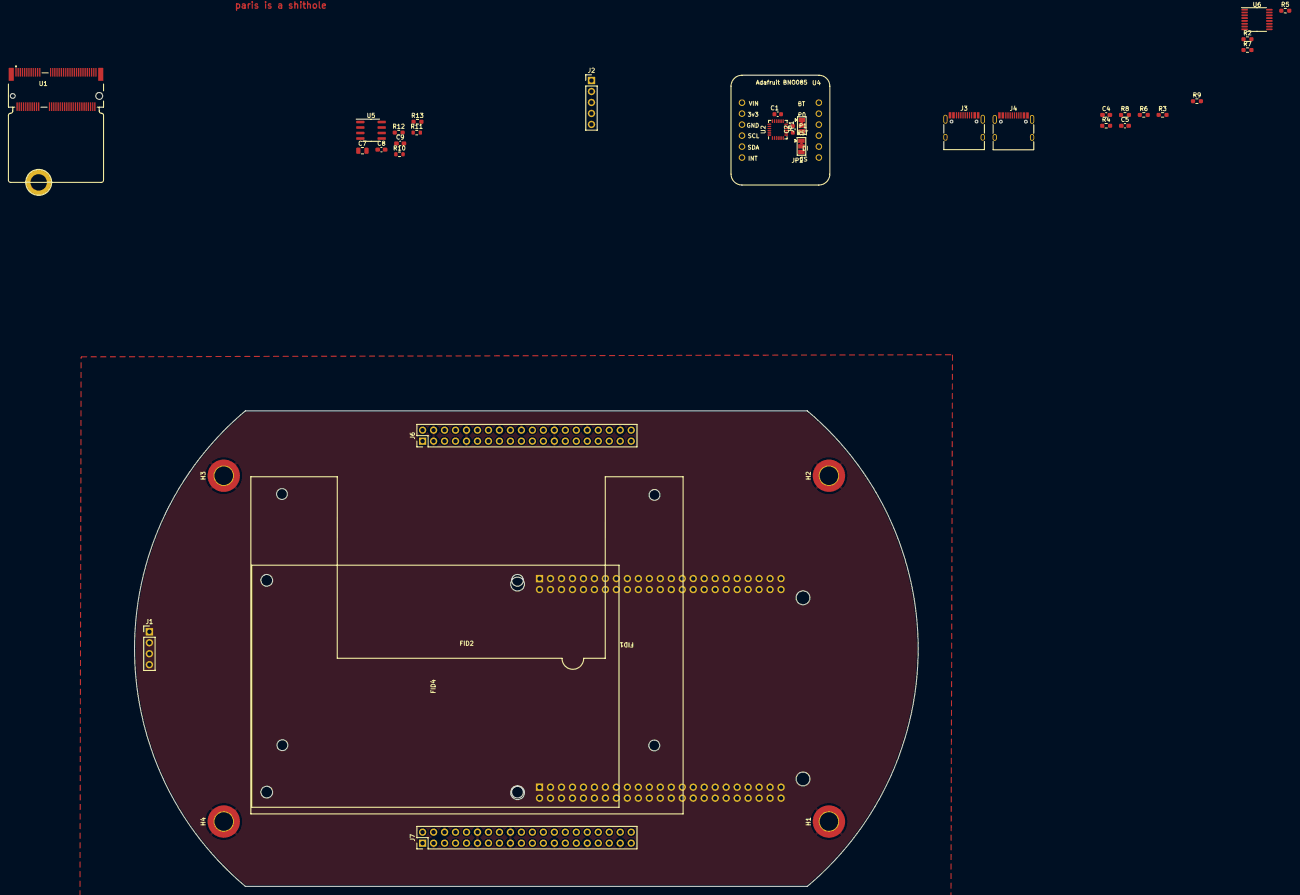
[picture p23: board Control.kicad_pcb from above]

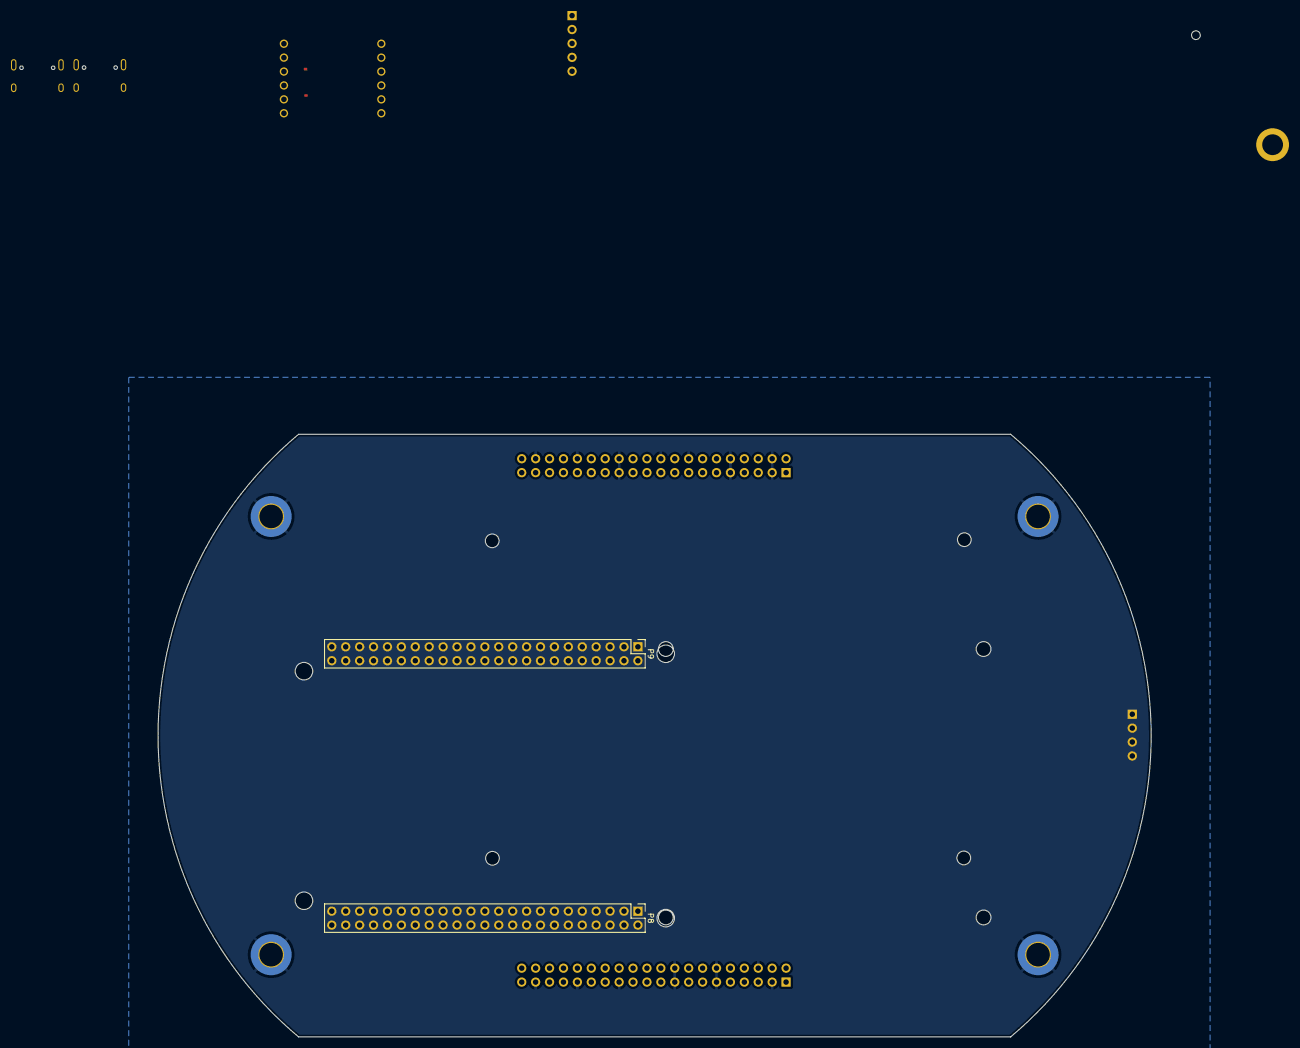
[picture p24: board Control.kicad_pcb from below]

Board: 2 copper layers, 181.3 x 110.0 mm, 45 parts (6 on the bottom side), 45 nets, no tracks yet.

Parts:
C1, C2: 100n; C_0603_1608Metric
C4, C8, C9: 100n; C_0603_1608Metric_Pad1.08x0.95mm_HandSolder
C5: 15p; C_0603_1608Metric_Pad1.08x0.95mm_HandSolder
C7: 22u; C_0805_2012Metric
FID1: Fiducial; AI-64
FID2: Fiducial; Jetson-NANO-mechanical
FID4: Fiducial; RPI4B-mechanical
H1, H2, H3, H4: Hole; MountingHole_4.3mm_M4_DIN965_Pad_TopBottom
J1: Ultrasonic Ranging; PinHeader_1x04_P2.54mm_Vertical
J2: Conn_01x05; PinHeader_1x05_P2.54mm_Vertical
J3: Output; USB_C_Receptacle_HRO_TYPE-C-31-M-12
J4: Input; USB_C_Receptacle_HRO_TYPE-C-31-M-12
J6: left; PinHeader_2x20_P2.54mm_Vertical
J7: right; PinHeader_2x20_P2.54mm_Vertical
JP1, JP2: set; SolderJumper-3_P1.3mm_Bridged12_Pad1.0x1.5mm
MH1, MH2, MH3, MH4: MountingHole_3.2mm_M3_DIN965
P8, P9: BeagleBone_Black_Header; PinHeader_2x23_P2.54mm_Vertical
R2: 2k7; R_0603_1608Metric_Pad0.98x0.95mm_HandSolder
R3, R4, R5, R6: 5k1; R_0603_1608Metric_Pad0.98x0.95mm_HandSolder
R7, R8: 1k; R_0603_1608Metric_Pad0.98x0.95mm_HandSolder
R9: 1Meg; R_0603_1608Metric_Pad0.98x0.95mm_HandSolder
R10, R11: 10k; R_0603_1608Metric
R12, R13: 120; R_0603_1608Metric_Pad0.98x0.95mm_HandSolder
U1: SparkFun-micromod; SparkFun-micromod-footprint
U2: MPU-6050; InvenSense_QFN-24_4x4mm_P0.5mm
U4: BNO085-breackout
U5: TJA1042T-3; SOIC-8_3.9x4.9mm_P1.27mm
U6: PCA9557PW; TSSOP-16_4.4x5mm_P0.65mm

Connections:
+3V3: C1.1, C2.1, C4.1, C9.1, J1.4, J2.5, J6.5, J6.6, J6.7, J6.8, J6.19, J6.31, J7.30, J7.38, JP1.3 (B), JP2.3 (B), P9.3, P9.4, R2.1, R7.1, R8.2, R10.1, R11.1, U1.2 (3v3), U1.74 (3V3), U2.8 (VDDIO), U2.13 (VDD), U4.1 (VIN), U5.5 (VIO), U6.16 (VDD)
+5V: C7.1, C8.1, J7.13, J7.14, J7.15, J7.16, P9.5, P9.6, U5.3 (VCC)
/CAN_H: R12.1, R13.1, U5.7 (CANH)
/CAN_L: R12.2, R13.2, U5.6 (CANL)
/Green_1: J6.29, U1.56 (AUD_OUT)
/Green_2: J6.17, U1.51 (I2C_SDA1)
/Green_3: J7.36, U1.52 (AUD_LRCLK)
/Green_4: J7.28, U1.17 (UART_TX1)
/INT_1: J2.2, U1.16 (I2C_INT), U2.12 (INT), U4.6 (INT)
/cc1: J3.A5 (CC1), J4.A5 (CC1), R3.1, R4.1
/cc2: J3.B5 (CC2), J4.B5 (CC2), R5.1, R6.1
/yellow_1: J6.27, U1.54 (AUD_IN)
/yellow_2: J6.15, U1.53 (I2C_SCL1)
/yellow_3: J7.34, U1.50 (AUD_BCLK)
/yellow_4: J7.26, U1.19 (UART_RX1)
AIN1_1: J6.39, U1.40 (G0/BUS0)
AIN1_2: J7.8, U1.48 (G4/BUS4)
AIN2_1: J6.37, U1.42 (G1/BUS1)
AIN2_2: J7.9, U1.44 (G2/BUS2)
BIN1_1: J6.34, U1.34 (A0)
BIN1_2: J7.5, U1.46 (G3/BUS3)
BIN2_1: J6.36, U1.38 (A1)
BIN2_2: J7.4, U1.73 (G5/BUS5)
D2+: J4.A6 (D+), J4.B6 (D+), U1.3 (USB_D+)
D2-: J4.A7 (D-), J4.B7 (D-), U1.5 (USB_D-)
D+: J3.A6 (D+), J3.B6 (D+)
D-: J3.A7 (D-), J3.B7 (D-)
GND: C1.2, C2.2, C4.2, C5.2, C7.2, C8.2, C9.2, H1.1, H2.1, H3.1, H4.1, J1.1, J2.1, J3.A1 (GND), J3.A12 (GND), J3.B1 (GND), J3.B12 (GND), J4.A1 (GND), J4.A12 (GND), J4.B1 (GND), J4.B12 (GND), J6.3, J6.4, J6.9, J6.10, J6.16, J6.20, J6.21, J6.25, J6.26, J6.32, J6.33, J6.38, J7.3, J7.6, J7.11, J7.12, J7.17, J7.18, J7.25, J7.31, J7.32, J7.37, J7.40, JP1.1 (A), JP2.1 (A), P8.1, P8.2, P8.45, P9.1, P9.2, P9.34, P9.43, P9.44, P9.45, P9.46, R3.2, R4.2, R5.2, R6.2, R9.1, U1.1 (GND), U1.7 (GND), U1.33 (GND), U1.36 (GND), U1.39 (GND), U1.45 (GND), U1.75 (GND), U2.18 (GND), U4.3 (GND), U5.2 (GND), U6.5 (A2), U6.8 (VSS)
unnamed: C5.1, J3.S1 (SHIELD), R9.2
unnamed: JP1.2 (C), U2.9 (AD0)
unnamed: JP2.2 (C), U4.8 (DI)
unnamed: R2.2, U6.15 (~RESET)
unnamed: R7.2, U6.3 (A0)
unnamed: R8.1, U6.4 (A1)
PWMA_1: J6.35, U1.10 (D0)
PWMA_2: J7.10, U1.18 (D1)
PWMB_1: J6.40, U1.32 (PWM0)
PWMB_2: J7.2, U1.47 (PWM1)
SCL: J1.3, J2.3, J6.1, P9.19, R10.2, U1.14 (I2C_SCL), U2.23 (SCL), U4.4 (SCL), U6.1 (SCL)
SDA: J1.2, J2.4, J6.2, P9.20, R11.2, U1.12 (I2C_SDA), U2.24 (SDA), U4.5 (SDA), U6.2 (SDA)
SPI_CS: P9.17, U1.55 (SPI_CS)
SPI_MISO: P9.29, U1.59 (SPI_COPI_(MOSI))
SPI_MOSI: P9.30, U1.61 (SPI_CIPO_(MISO))
SPI_SCK: P9.31, U1.57 (SPI_SCK)
VBUS: J3.A4 (VBUS), J3.A9 (VBUS), J3.B4 (VBUS), J3.B9 (VBUS), J4.A4 (VBUS), J4.A9 (VBUS), J4.B4 (VBUS), J4.B9 (VBUS), P9.7, P9.8

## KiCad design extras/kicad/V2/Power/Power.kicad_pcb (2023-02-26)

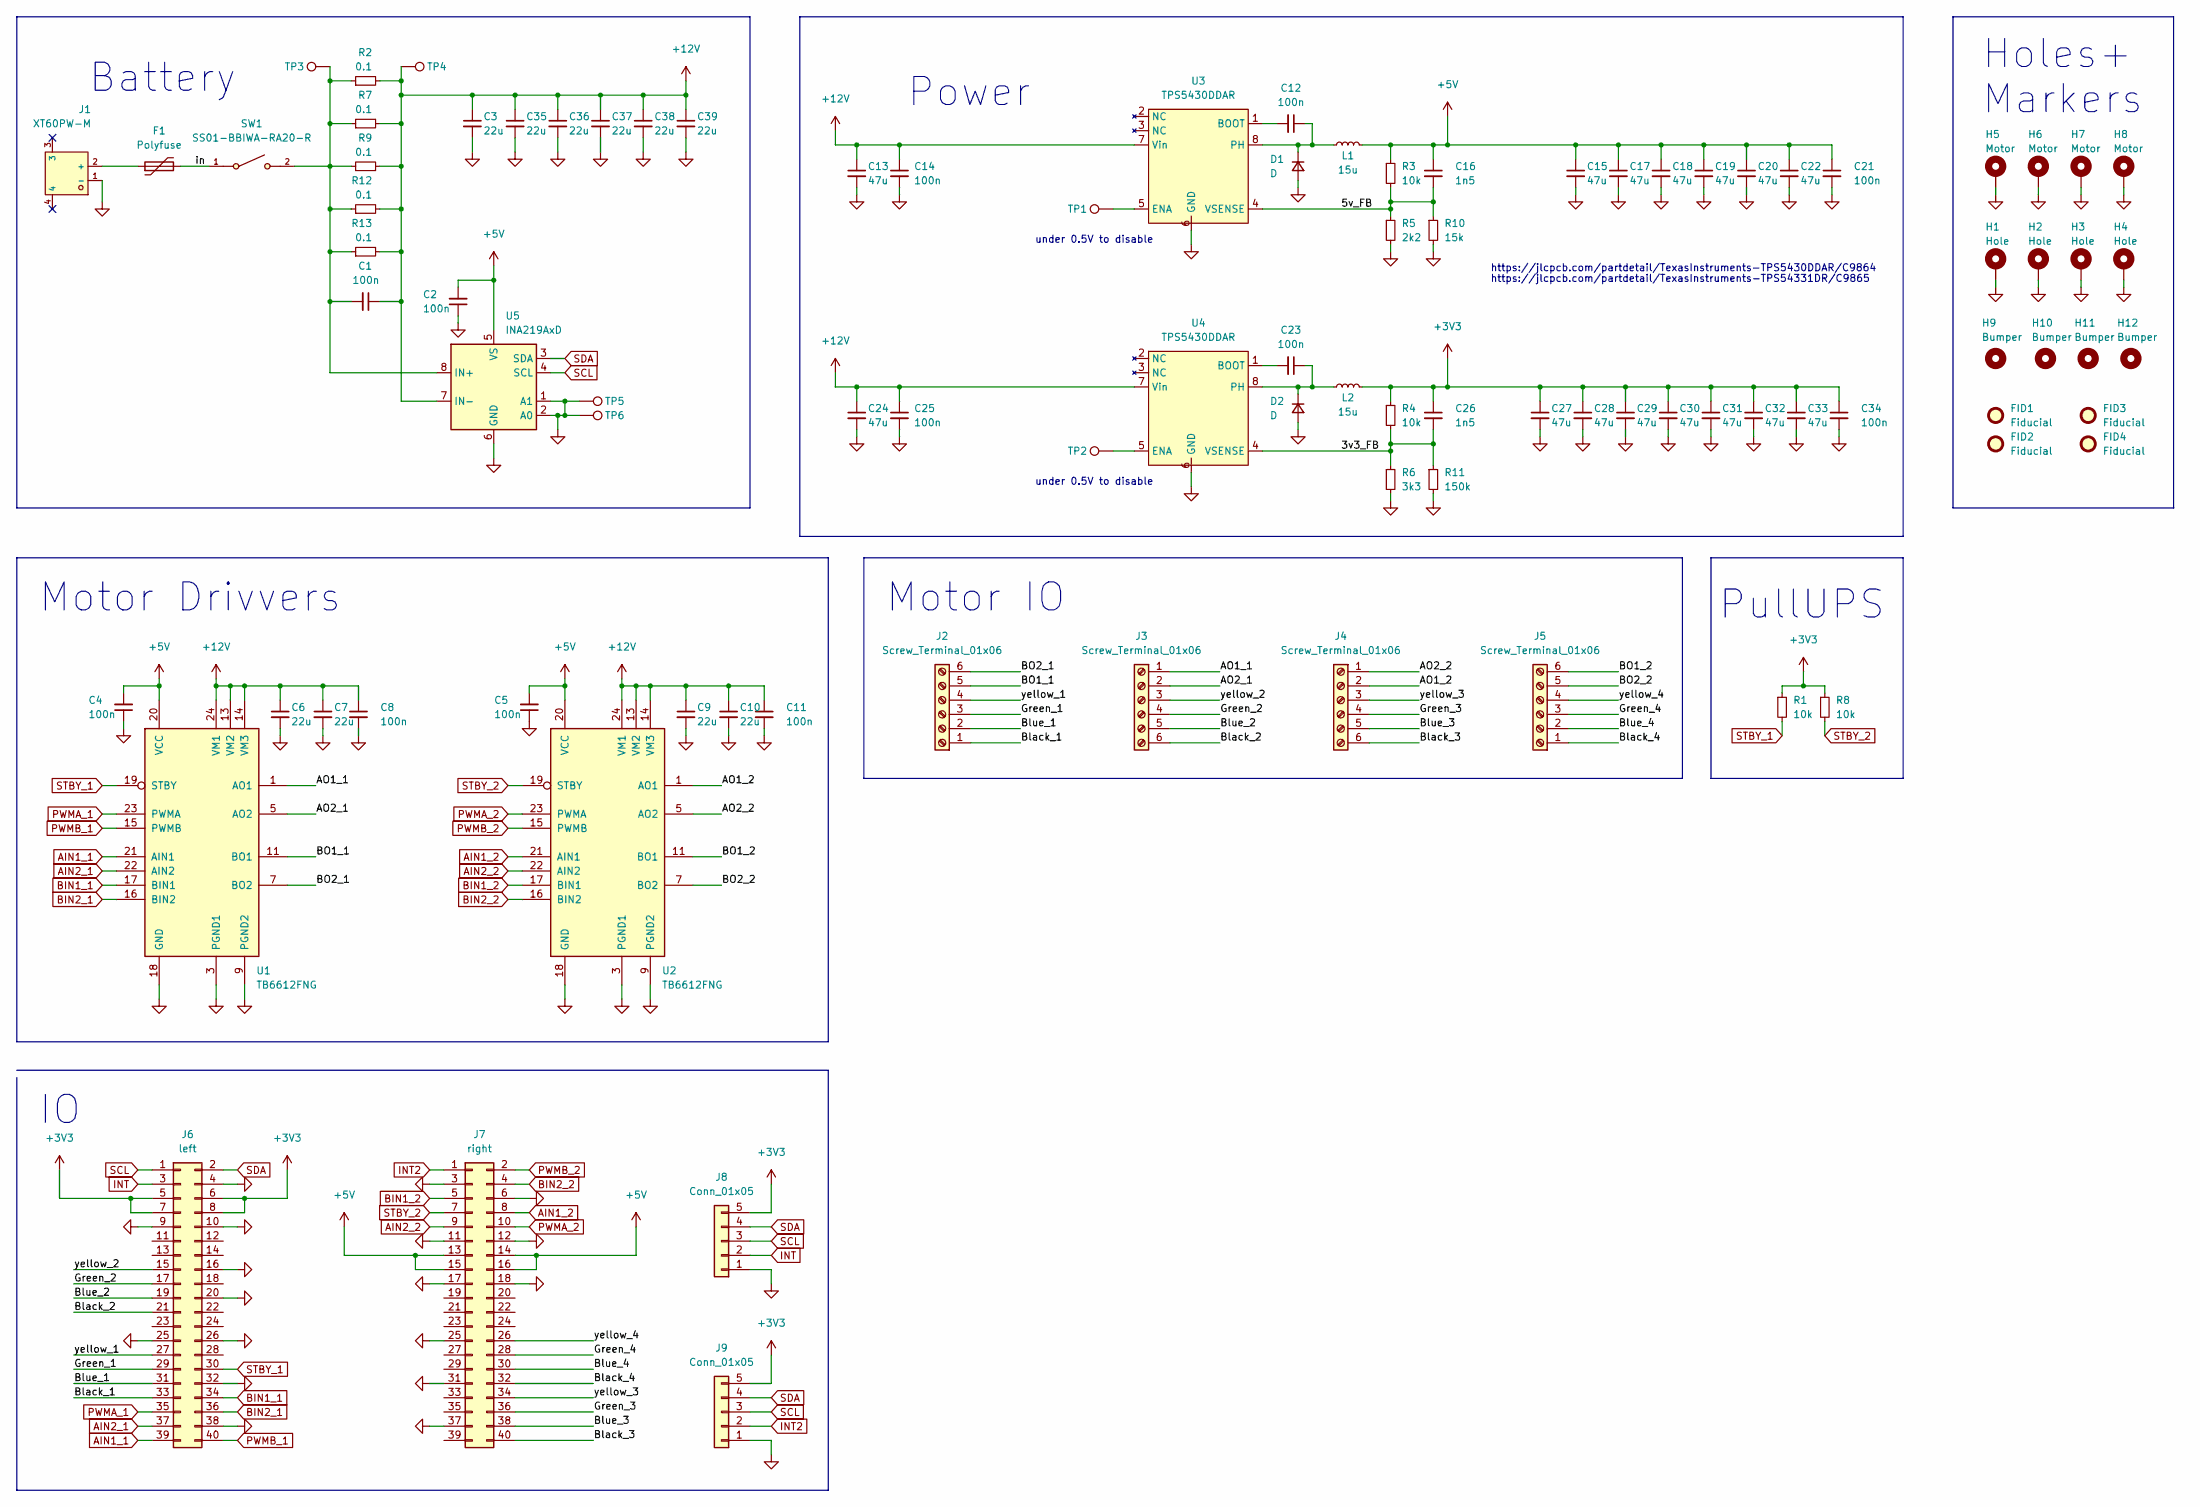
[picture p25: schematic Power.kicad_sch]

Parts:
C1, C2, C4, C5, C8, C11, C12, C14, C21, C23, C25, C34: 100n; C_0603_1608Metric; LCSC C14663
C3, C6, C7, C9, C10, C35, C36, C37, C38, C39: 22u; C_0805_2012Metric; LCSC C45783
C13, C15, C17, C18, C19, C20, C22, C24, C27, C28, C29, C30, C31, C32, C33: 47u; C_1206_3216Metric; LCSC C96123
C16, C26: 1n5; C_0603_1608Metric_Pad1.08x0.95mm_HandSolder; LCSC C1595
D1, D2: D; D_SMA; LCSC C22452
F1: Polyfuse; Fuse_2920_7451Metric_Pad2.10x5.45mm_HandSolder
FID1: Fiducial; Fiducial_0.5mm_Mask1mm
FID2: Fiducial; WEEE-Logo_5.6x8mm_SilkScreen
FID3: Fiducial; OSHW-Logo2_14.6x12mm_SilkScreen
FID4: Fiducial; KiCad-Logo2_6mm_SilkScreen
H1, H2, H3, H4: Hole; MountingHole_4.3mm_M4_DIN965_Pad_TopBottom
H5, H6, H7, H8: Motor; JGA25-370 DC motor
H9, H10, H11, H12: Bumper; MountingHole_4.5mm
J1: XT60PW-M; CONN-TH_XT60PW-M; LCSC C98732
J2, J3, J4, J5: Screw_Terminal_01x06; TerminalBlock_4Ucon_1x06_P3.50mm_Horizontal
J6: left; PinHeader_2x20_P2.54mm_Vertical
J7: right; PinHeader_2x20_P2.54mm_Vertical
J8, J9: Conn_01x05; PinHeader_1x05_P2.54mm_Vertical
L1, L2: 15u; Inductor SMD,11.6x10.1x4mm; LCSC C3002687
R1, R3, R4, R8: 10k; R_0603_1608Metric; LCSC C25804
R2, R7, R9, R12, R13: 0.1; R_1206_3216Metric_Pad1.30x1.75mm_HandSolder; LCSC C25334
R5: 2k2; R_0603_1608Metric_Pad0.98x0.95mm_HandSolder; LCSC C4190
R6: 3k3; R_0603_1608Metric_Pad0.98x0.95mm_HandSolder; LCSC C22978
R10: 15k; R_0603_1608Metric_Pad0.98x0.95mm_HandSolder; LCSC C22809
R11: 150k; R_0603_1608Metric_Pad0.98x0.95mm_HandSolder; LCSC C22807
SW1: SS01-BBIWA-RA20-R; SW-TH_SS01-BBIWA-RA20-R; LCSC C309065
TP1, TP2, TP3, TP4, TP5, TP6: TestPoint; TestPoint_Pad_D1.0mm
U1, U2: TB6612FNG; SSOP-24_5.3x8.2mm_P0.65mm; LCSC C88224
U3, U4: TPS5430DDAR; SOIC-8-1EP_3.9x4.9mm_P1.27mm_EP2.29x3mm_ThermalVias; LCSC C9864
U5: INA219AxD; SOIC-8_3.9x4.9mm_P1.27mm; LCSC C138706

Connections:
+3V3: C26.1, C27.1, C28.1, C29.1, C30.1, C31.1, C32.1, C33.1, C34.1, J6.5, J6.6, J6.7, J6.8, J8.5, J9.5, L2.2, R1.1, R4.1, R8.1
+5V: C2.2, C4.2, C5.2, C15.1, C16.1, C17.1, C18.1, C19.1, C20.1, C21.1, C22.1, J7.13, J7.14, J7.15, J7.16, L1.2, R3.1, U1.20 (VCC), U2.20 (VCC), U5.5 (VS)
+12V: C1.1, C3.1, C6.1, C7.1, C8.1, C9.1, C10.1, C11.1, C13.1, C14.1, C24.1, C25.1, C35.1, C36.1, C37.1, C38.1, C39.1, R2.2, R7.2, R9.2, R12.2, R13.2, TP4.1, U1.13 (VM2), U1.14 (VM3), U1.24 (VM1), U2.13 (VM2), U2.14 (VM3), U2.24 (VM1), U3.7 (Vin), U4.7 (Vin), U5.7 (IN-)
/3v3_FB: C26.2, R4.2, R6.1, R11.1, U4.4 (VSENSE)
/5v_FB: C16.2, R3.2, R5.1, R10.1, U3.4 (VSENSE)
/AO1_1: J3.1, U1.1 (AO1), U1.2 (AO1)
/AO1_2: J4.2, U2.1 (AO1), U2.2 (AO1)
/AO2_1: J3.2, U1.5 (AO2), U1.6 (AO2)
/AO2_2: J4.1, U2.5 (AO2), U2.6 (AO2)
/BO1_1: J2.5, U1.11 (BO1), U1.12 (BO1)
/BO1_2: J5.6, U2.11 (BO1), U2.12 (BO1)
/BO2_1: J2.6, U1.7 (BO2), U1.8 (BO2)
/BO2_2: J5.5, U2.7 (BO2), U2.8 (BO2)
/Black_1: J2.1, J6.33
/Black_2: J3.6, J6.21
/Black_3: J4.6, J7.40
/Black_4: J5.1, J7.32
/Blue_1: J2.2, J6.31
/Blue_2: J3.5, J6.19
/Blue_3: J4.5, J7.38
/Blue_4: J5.2, J7.30
/Green_1: J2.3, J6.29
/Green_2: J3.4, J6.17
/Green_3: J4.4, J7.36
/Green_4: J5.3, J7.28
/in: F1.2, SW1.1
/yellow_1: J2.4, J6.27
/yellow_2: J3.3, J6.15
/yellow_3: J4.3, J7.34
/yellow_4: J5.4, J7.26
AIN1_1: J6.39, U1.21 (AIN1)
AIN1_2: J7.8, U2.21 (AIN1)
AIN2_1: J6.37, U1.22 (AIN2)
AIN2_2: J7.9, U2.22 (AIN2)
BIN1_1: J6.34, U1.17 (BIN1)
BIN1_2: J7.5, U2.17 (BIN1)
BIN2_1: J6.36, U1.16 (BIN2)
BIN2_2: J7.4, U2.16 (BIN2)
GND: C2.1, C3.2, C4.1, C5.1, C6.2, C7.2, C8.2, C9.2, C10.2, C11.2, C13.2, C14.2, C15.2, C17.2, C18.2, C19.2, C20.2, C21.2, C22.2, C24.2, C25.2, C27.2, C28.2, C29.2, C30.2, C31.2, C32.2, C33.2, C34.2, C35.2, C36.2, C37.2, C38.2, C39.2, D1.2 (A), D2.2 (A), H1.1, H2.1, H3.1, H4.1, H5.1, H6.1, H7.1, H8.1, J1.1 (-), J6.4, J6.9, J6.10, J6.16, J6.20, J6.25, J6.26, J6.32, J6.38, J7.3, J7.6, J7.11, J7.12, J7.17, J7.18, J7.25, J7.31, J7.37, J8.1, J9.1, R5.2, R6.2, R10.2, R11.2, TP5.1, TP6.1, U1.3 (PGND1), U1.4 (PGND1), U1.9 (PGND2), U1.10 (PGND2), U1.18 (GND), U2.3 (PGND1), U2.4 (PGND1), U2.9 (PGND2), U2.10 (PGND2), U2.18 (GND), U3.6 (GND), U3.9 (Thermal), U4.6 (GND), U4.9 (Thermal), U5.1 (A1), U5.2 (A0), U5.6 (GND)
INT: J6.3, J8.2
INT2: J7.1, J9.2
unnamed: C1.2, R2.1, R7.1, R9.1, R12.1, R13.1, SW1.2, TP3.1, U5.8 (IN+)
unnamed: C12.1, D1.1 (K), L1.1, U3.8 (PH)
unnamed: C12.2, U3.1 (BOOT)
unnamed: C23.1, D2.1 (K), L2.1, U4.8 (PH)
unnamed: C23.2, U4.1 (BOOT)
unnamed: F1.1, J1.2 (+)
unnamed: TP1.1, U3.5 (ENA)
unnamed: TP2.1, U4.5 (ENA)
PWMA_1: J6.35, U1.23 (PWMA)
PWMA_2: J7.10, U2.23 (PWMA)
PWMB_1: J6.40, U1.15 (PWMB)
PWMB_2: J7.2, U2.15 (PWMB)
SCL: J6.1, J8.3, J9.3, U5.4 (SCL)
SDA: J6.2, J8.4, J9.4, U5.3 (SDA)
STBY_1: J6.30, R1.2, U1.19 (STBY)
STBY_2: J7.7, R8.2, U2.19 (STBY)

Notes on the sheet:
Motor IO
https://jlcpcb.com/partdetail/TexasInstruments-TPS5430DDAR/C9864
Motor Drivvers
https://jlcpcb.com/partdetail/TexasInstruments-TPS54331DR/C9865
under 0.5V to disable
PullUPS
Holes+ Markers
Battery
Power

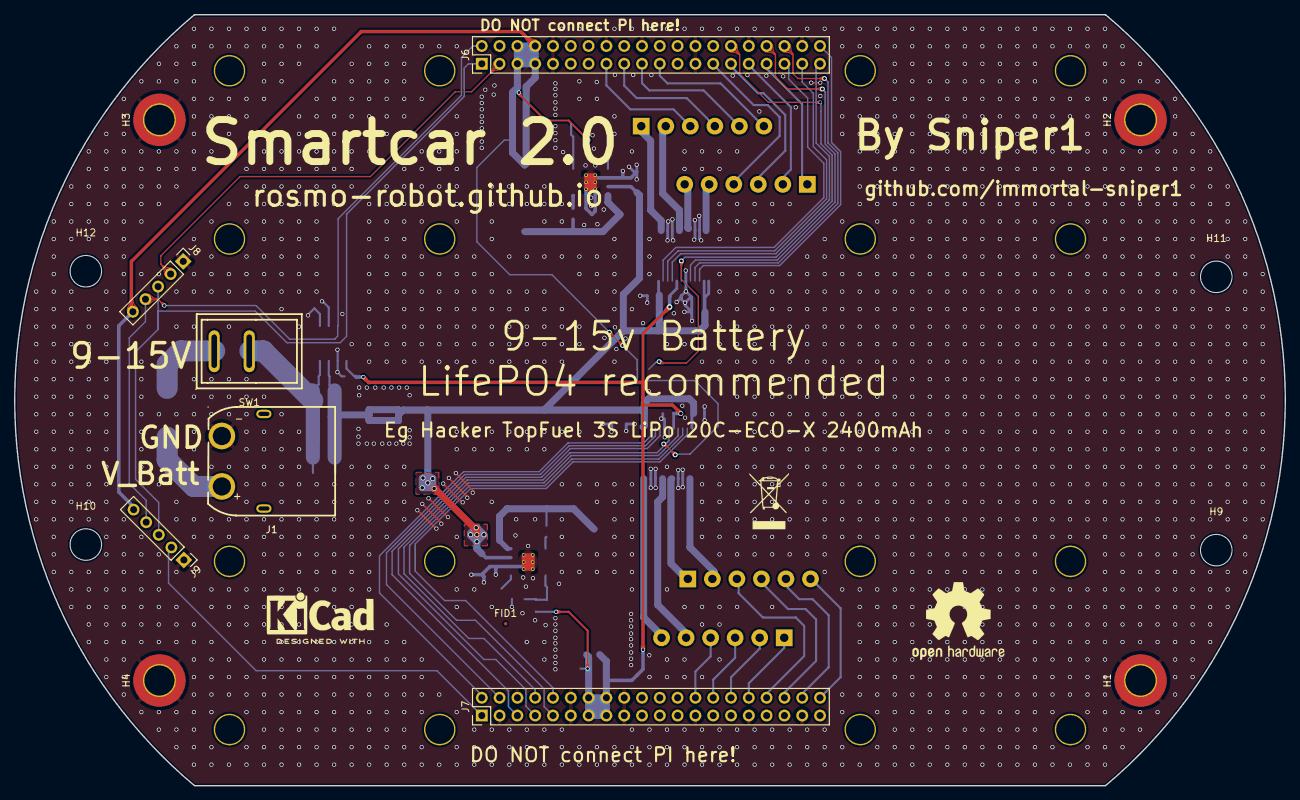
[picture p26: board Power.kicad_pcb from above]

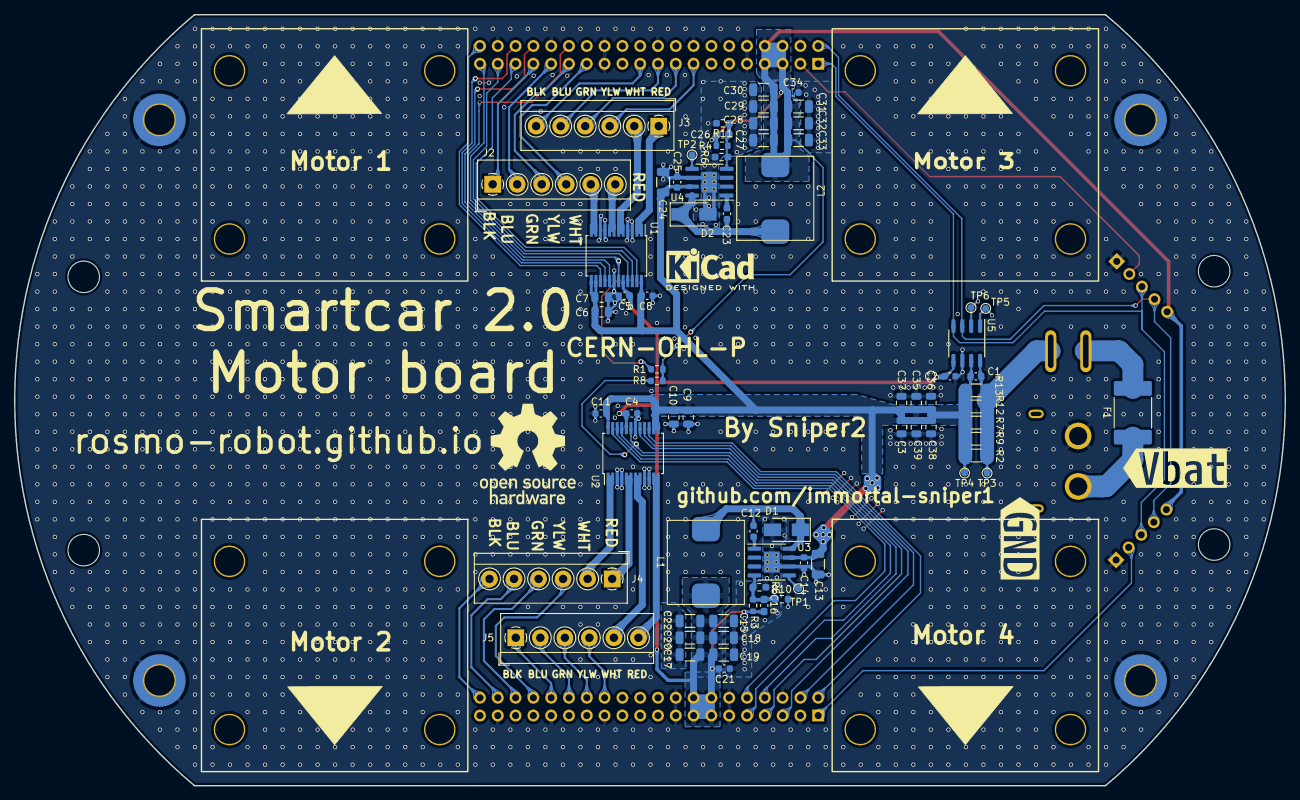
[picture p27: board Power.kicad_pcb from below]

Board: 2 copper layers, 181.3 x 110.0 mm, 96 parts (78 on the bottom side), 57 nets.

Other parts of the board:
kibuzzard-63E93541: G***; kibuzzard-63E93541
kibuzzard-63E93553: G***; kibuzzard-63E93553

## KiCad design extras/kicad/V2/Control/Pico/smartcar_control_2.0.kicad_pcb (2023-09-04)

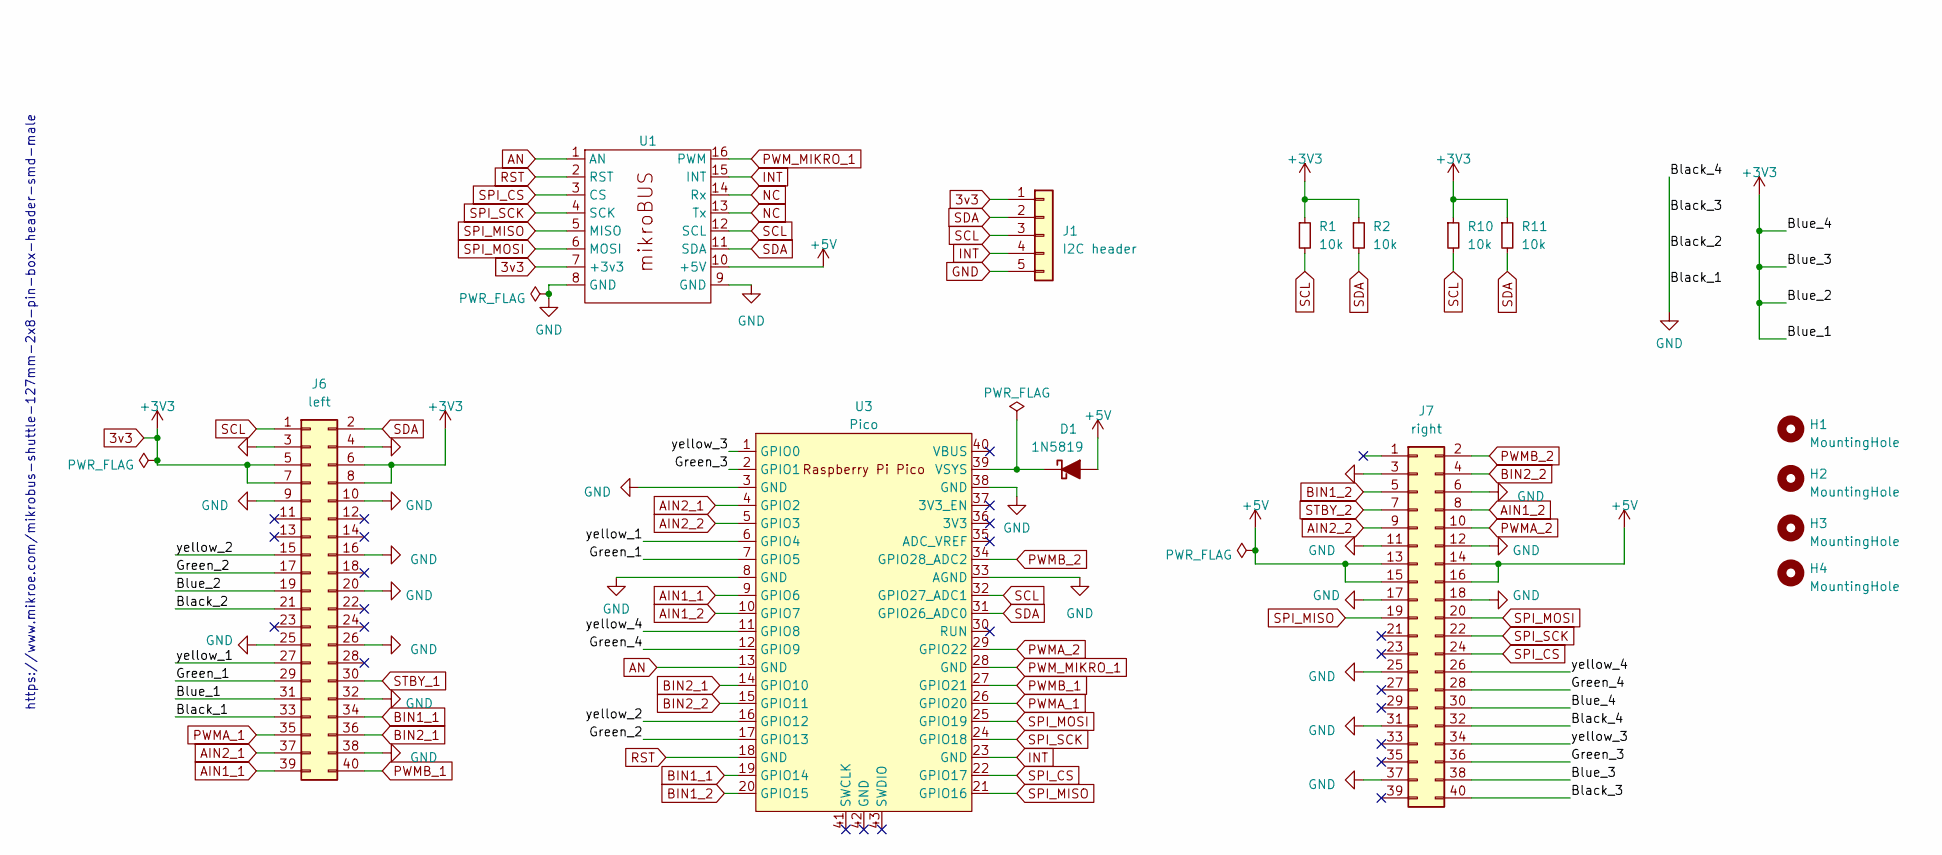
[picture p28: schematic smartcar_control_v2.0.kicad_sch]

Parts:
D1: 1N5819; D_DO-41_SOD81_P7.62mm_Horizontal; LCSC C698893
H1, H2, H3, H4: MountingHole; MountingHole_3.2mm_M3
J1: I2C header; PinHeader_1x05_P2.54mm_Vertical
J6: left; PinHeader_2x20_P2.54mm_Vertical
J7: right; PinHeader_2x20_P2.54mm_Vertical
R1, R2: 10k; R_Axial_DIN0207_L6.3mm_D2.5mm_P7.62mm_Horizontal
R10, R11: 10k; R_0603_1608Metric; LCSC C25804
U1: mikroBUS
U3: Pico; RPi_Pico_SMD_TH

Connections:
3v3: J1.1, J6.5, J6.6, J6.7, J6.8, J6.19, J6.31, J7.30, J7.38, R1.1, R2.1, R10.1, R11.1, U1.7 (+3v3)
+5V: D1.2 (A), J7.13, J7.14, J7.15, J7.16, U1.10 (+5V)
/Green_1: J6.29, U3.7 (GPIO5)
/Green_2: J6.17, U3.17 (GPIO13)
/Green_3: J7.36, U3.2 (GPIO1)
/Green_4: J7.28, U3.12 (GPIO9)
/yellow_1: J6.27, U3.6 (GPIO4)
/yellow_2: J6.15, U3.16 (GPIO12)
/yellow_3: J7.34, U3.1 (GPIO0)
/yellow_4: J7.26, U3.11 (GPIO8)
AIN1_1: J6.39, U3.9 (GPIO6)
AIN1_2: J7.8, U3.10 (GPIO7)
AIN2_1: J6.37, U3.4 (GPIO2)
AIN2_2: J7.9, U3.5 (GPIO3)
AN: U1.1 (AN), U3.13 (GND)
BIN1_1: J6.34, U3.19 (GPIO14)
BIN1_2: J7.5, U3.20 (GPIO15)
BIN2_1: J6.36, U3.14 (GPIO10)
BIN2_2: J7.4, U3.15 (GPIO11)
GND: J1.5, J6.3, J6.4, J6.9, J6.10, J6.16, J6.20, J6.21, J6.25, J6.26, J6.32, J6.33, J6.38, J7.3, J7.6, J7.11, J7.12, J7.17, J7.18, J7.25, J7.31, J7.32, J7.37, J7.40, U1.8 (GND), U1.9 (GND), U3.3 (GND), U3.8 (GND), U3.33 (AGND), U3.38 (GND)
INT: J1.4, U1.15 (INT), U3.23 (GND)
NC: U1.13 (Tx), U1.14 (Rx)
unnamed: D1.1 (K), U3.39 (VSYS)
PWMA_1: J6.35, U3.26 (GPIO20)
PWMA_2: J7.10, U3.29 (GPIO22)
PWMB_1: J6.40, U3.27 (GPIO21)
PWMB_2: J7.2, U3.34 (GPIO28_ADC2)
PWM_MIKRO_1: U1.16 (PWM), U3.28 (GND)
RST: U1.2 (RST), U3.18 (GND)
SCL: J1.3, J6.1, R1.2, R10.2, U1.12 (SCL), U3.32 (GPIO27_ADC1)
SDA: J1.2, J6.2, R2.2, R11.2, U1.11 (SDA), U3.31 (GPIO26_ADC0)
SPI_CS: J7.24, U1.3 (CS), U3.22 (GPIO17)
SPI_MISO: J7.19, U1.5 (MISO), U3.21 (GPIO16)
SPI_MOSI: J7.20, U1.6 (MOSI), U3.25 (GPIO19)
SPI_SCK: J7.22, U1.4 (SCK), U3.24 (GPIO18)
STBY_1: J6.30
STBY_2: J7.7

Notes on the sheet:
https://www.mikroe.com/mikrobus-shuttle-127mm-2x8-pin-box-header-smd-male

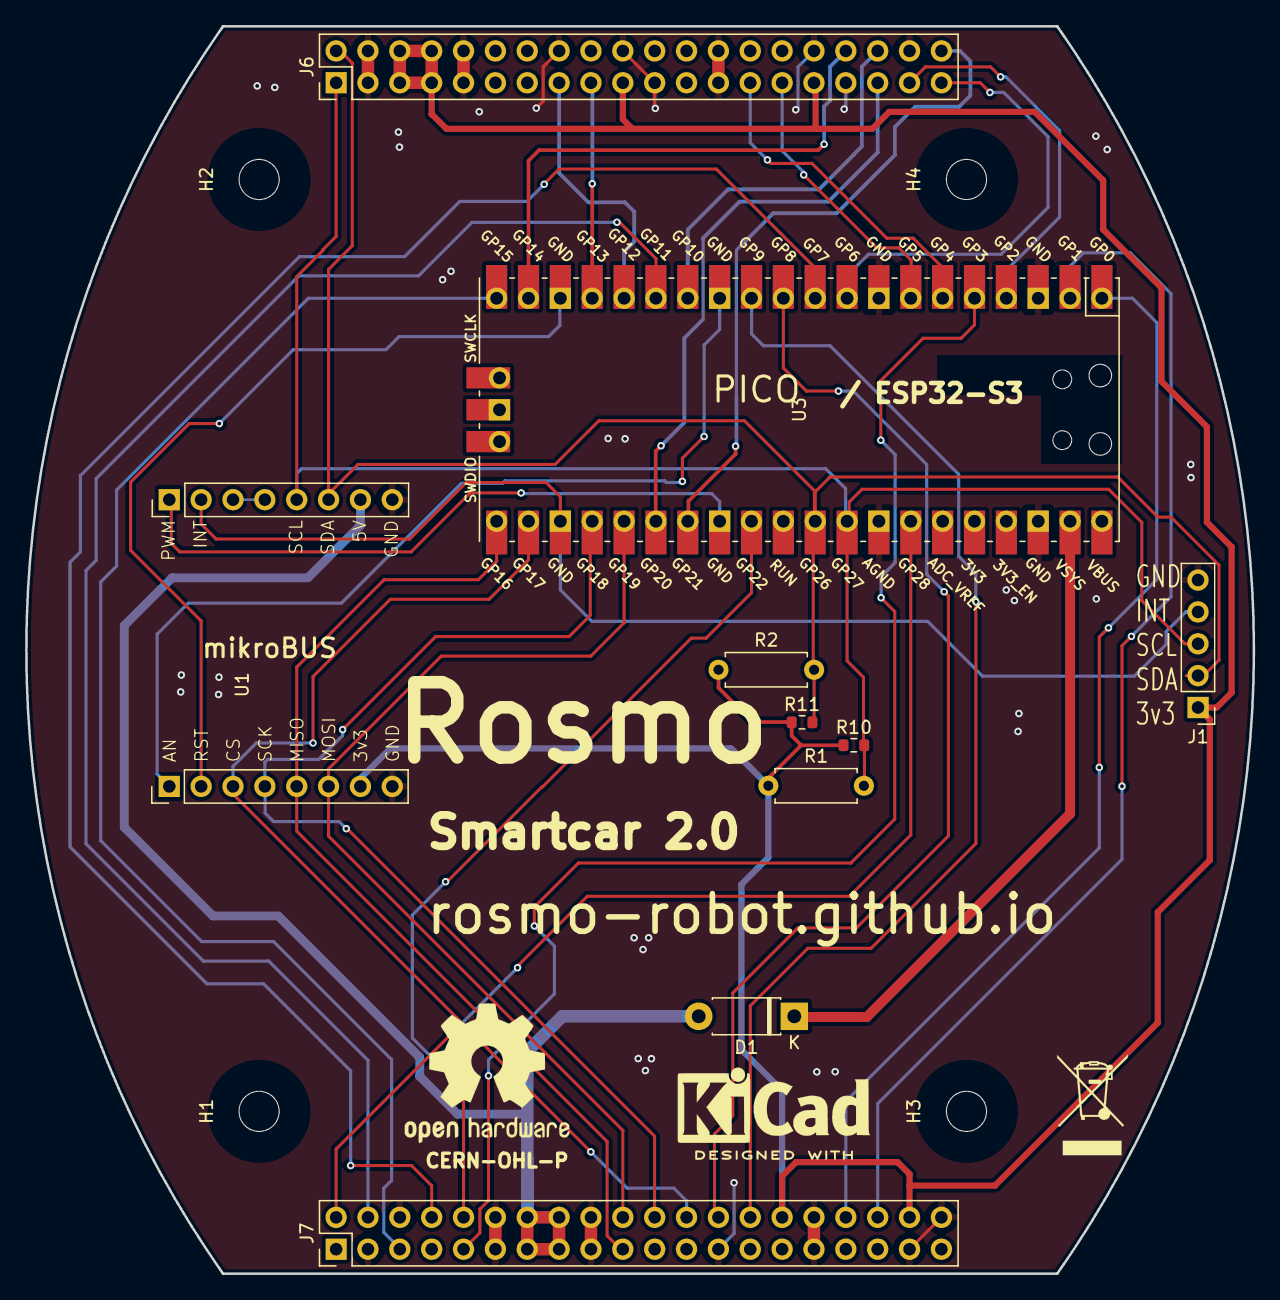
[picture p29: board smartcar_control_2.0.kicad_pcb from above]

Board: 2 copper layers, 97.9 x 99.4 mm, 17 parts (0 on the bottom side), 35 nets.

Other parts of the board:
FID2: Fiducial; WEEE-Logo_5.6x8mm_SilkScreen
FID3: Fiducial; OSHW-Logo2_14.6x12mm_SilkScreen
FID4: Fiducial; KiCad-Logo2_6mm_SilkScreen

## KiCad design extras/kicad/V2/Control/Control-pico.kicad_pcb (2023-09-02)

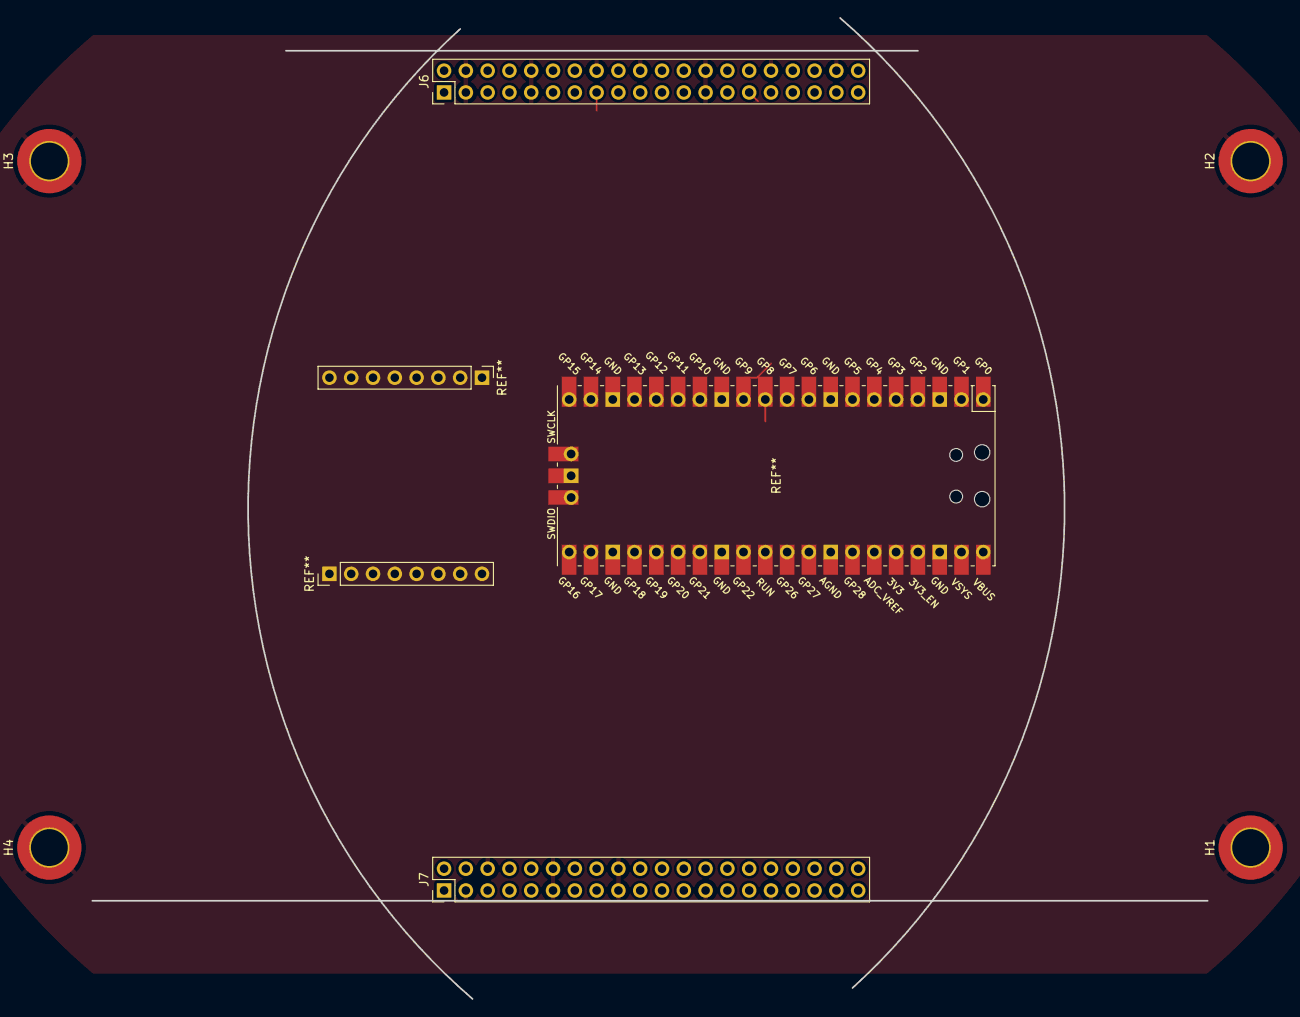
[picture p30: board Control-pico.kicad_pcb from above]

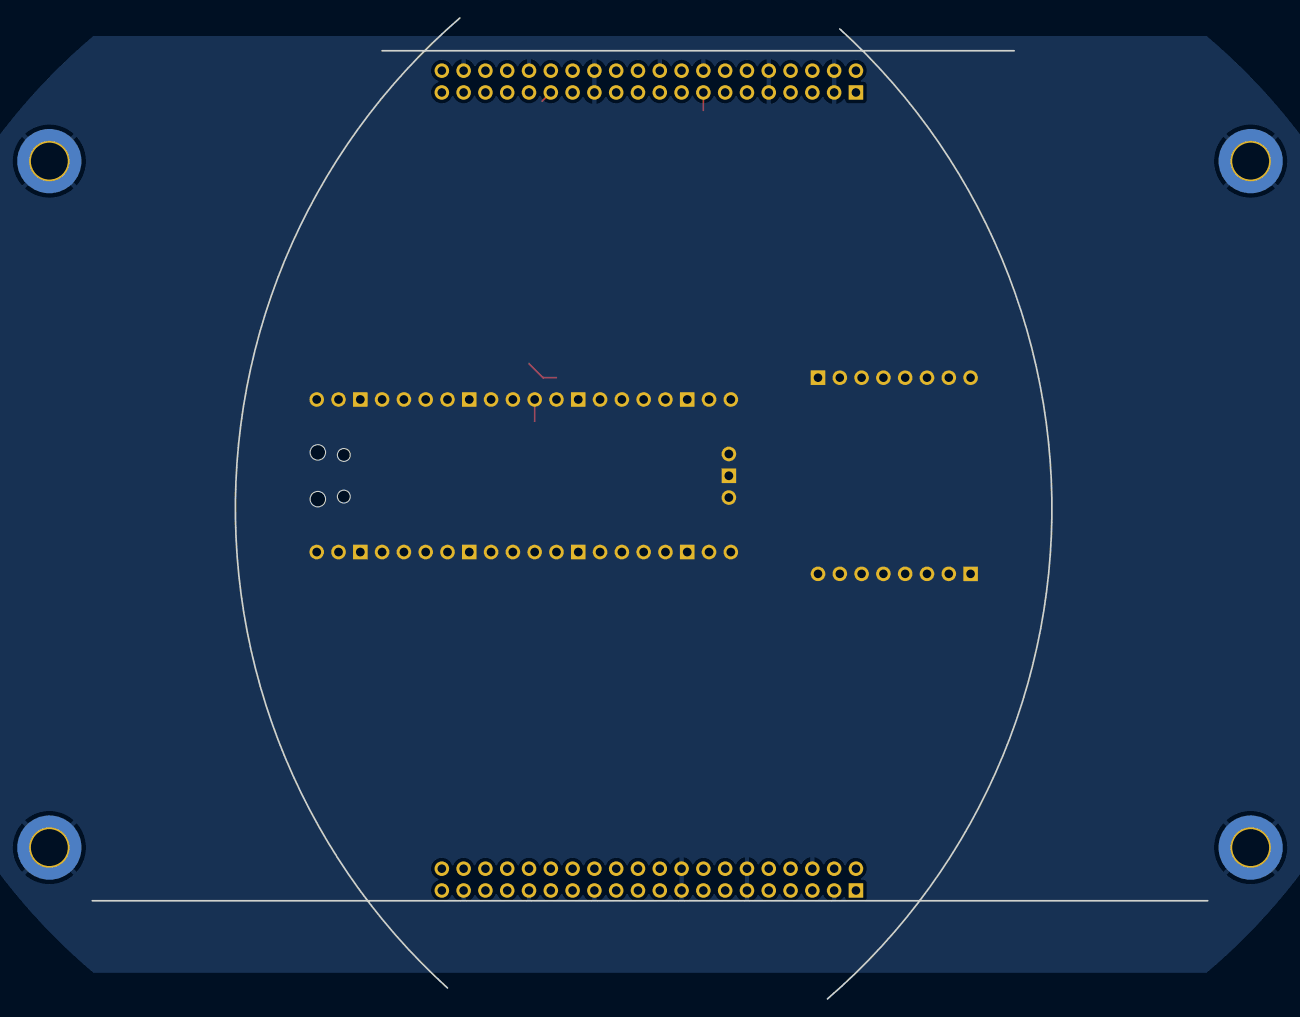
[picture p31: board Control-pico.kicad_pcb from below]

Board: 2 copper layers, 130.0 x 114.3 mm, 8 parts (2 on the bottom side), 3 nets.

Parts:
H1, H2, H3, H4: Hole; MountingHole_4.3mm_M4_DIN965_Pad_TopBottom
J6: left; PinHeader_2x20_P2.54mm_Vertical
J7: right; PinHeader_2x20_P2.54mm_Vertical
MH1, MH2: MountingHole_3.2mm_M3_DIN965

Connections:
+3V3: J6.5, J6.6, J6.7, J6.8, J6.19, J6.31, J7.30, J7.38
+5V: J7.13, J7.14, J7.15, J7.16
GND: H1.1, H2.1, H3.1, H4.1, J6.3, J6.4, J6.9, J6.10, J6.16, J6.20, J6.21, J6.25, J6.26, J6.32, J6.33, J6.38, J7.3, J7.6, J7.11, J7.12, J7.17, J7.18, J7.25, J7.31, J7.32, J7.37, J7.40

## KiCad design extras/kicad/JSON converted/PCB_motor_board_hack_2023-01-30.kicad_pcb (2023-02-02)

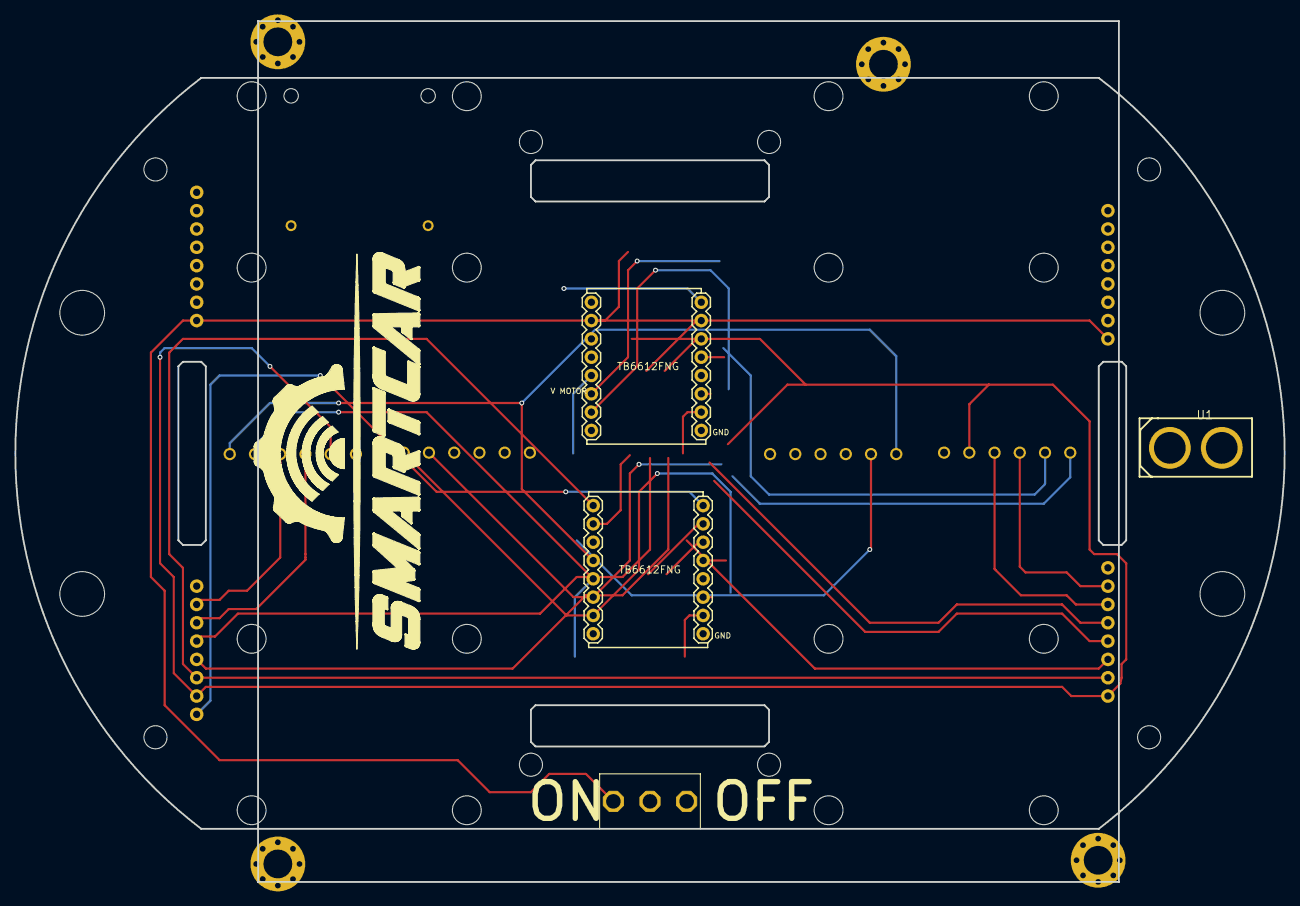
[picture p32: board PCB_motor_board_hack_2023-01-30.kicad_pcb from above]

Board: 2 copper layers, 176.0 x 119.4 mm, 25 parts (0 on the bottom side), 18 nets.

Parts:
1: NANO-ITX_120X120
J1, J2, J3, J4: 1X08_NO_SILK
J5, J6, J7, J8: 1X08
LOGO1, LOGO2: OSHW-LOGOL; OSHW-LOGO-L
MOTOR2, MOTOR3, MOTOR4, MOTOR5: SMARTCAR_MOTOR; SMARTCAR_MOTOR_MOUNT_HOLES
SMRTCR1: SMARTCAR_LOGOMEDIUM; SMARTCAR_LOGO_MEDIUM
SW1: SPDT-HIGH-AMP-SWITCHPTH; SPDT-0.2-THICK-PINS
U1: CONN-TH_XT60
U8: POLULUMOTORBRACKETPPCB
U$1, U$2: BUMPER_020522_SCREWS; BUMPER_2_SCREWS_NARROW
X1, X2, X3, X4: 6; 1751280

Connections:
BAT_GND: J1.1, J3.1, SW1.POS1
EN_L_1: J2.7, X1.4
EN_L_2: J2.6, X1.3
EN_R_1: J4.7, X3.4
EN_R_2: J4.6, X3.3
GND: J2.8, J4.8, J5.3, J5.8, J6.1, J7.1, J8.3, J8.8, SW1.SIG, X1.1, X3.1
MOTOR_L_EN: J2.1, J6.8, J7.8
MOTOR_L_IN1: J2.4, J6.6, J7.6
MOTOR_L_IN2: J2.5, J6.7, J7.7
MOTOR_L_OUT1: J5.4, J8.4, X1.6, X4.1
MOTOR_L_OUT2: J5.5, J8.5, X1.5, X4.2
MOTOR_R_EN: J4.3, J6.2, J7.2
MOTOR_R_IN1: J4.5, J6.4, J7.4
MOTOR_R_IN2: J4.4, J6.3, J7.3
MOTOR_R_OUT1: J5.7, J8.7, X2.1, X3.6
MOTOR_R_OUT2: J5.6, J8.6, X2.2, X3.5
MOTOR_VCC: J2.3, J4.2, J5.1, J8.1
VCC: J2.2, J4.1, J5.2, J6.5, J7.5, J8.2, X1.2, X3.2

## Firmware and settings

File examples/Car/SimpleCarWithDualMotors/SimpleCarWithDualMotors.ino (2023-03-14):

#include <Smartcar.h>

ArduinoRuntime arduinoRuntime;
const BrushedMotorPins leftFrontMotorPins{ 12, 14, 13 };
const BrushedMotorPins leftRearMotorPins{ 22, 24, 23 };
const BrushedMotorPins rightFrontMotorPins{ 25, 26, 27 };
const BrushedMotorPins rightRearMotorPins{ 32, 34, 33 };

BrushedMotor leftFrontMotor{ arduinoRuntime, leftFrontMotorPins };
BrushedMotor leftRearMotor{ arduinoRuntime, leftRearMotorPins };
BrushedMotor rightFrontMotor{ arduinoRuntime, rightFrontMotorPins };
BrushedMotor rightRearMotor{ arduinoRuntime, rightRearMotorPins };

DualMotor leftMotor{ leftFrontMotor, leftRearMotor };
DualMotor rightMotor{ rightFrontMotor, rightRearMotor };

DifferentialControl control{ leftMotor, rightMotor };

SimpleCar car{ control };

void setup()
{
    // Move forward for 3 seconds
    car.setSpeed(50);
    delay(3000);
    // Start turning sharp left
    car.setAngle(-90);
    delay(3000);
    // Straighten the car and move backward
    car.setAngle(0);
    car.setSpeed(-50);
    delay(3000);
    car.setSpeed(0);
}

void loop() {}

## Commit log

2023-01-28 Incomplete draft
    [modules_board.kicad_sch]
2023-01-28 Just outlines routing not done
    [motor_board2.0.kicad_pcb]
2023-01-30 Add BNO-85
    [modules_board2.0.kicad_sch]
2023-01-31 Upload Waffle plates from Turtlebot3
    https://www.turtlebot.com/turtlebot3/
    [TB3_Waffle_Plate-IPL-01.dwg]
2023-02-02 Messy schematic - Includes components
    Incomplete schematic that shows all the components on the Control/Modules board
2023-02-11 Version With Silkscreen
    Added here so as to not conflict with the /v2 folder
    [Power.kicad_pcb]
2023-02-21 Update BOM-Power.csv
    Added some LCSC part numbers
    [BOM-Power.csv]
2023-02-26 BNO085 footprint
2023-02-26 BNO85 footprint and schematic
2023-02-27 added 2242 footprint
    [Control.kicad_pcb]
2023-02-28 BLDC version
2023-02-28 Added UEXT, Mikroe & 7Pin SPI
    (7pin SPI is break out garden) so we don't forget them
    [Control.kicad_sch]
2023-02-28 Added links to parts
    [Control.kicad_sch]
2023-03-03 Minor schematic change
    t
    [Control.kicad_sch]
2023-03-04 Added control-sam
    A
    [ControlSam.kicad_pcb]
2023-03-04 Added larger M.2 & Mikro click board footprints
    [Control.kicad_pcb, ControlSam.kicad_pcb]
2023-03-11 Draft of schematic - needs tidying
2023-03-20 Idea for Mikro
    Rough PCB & Schematic
    [ControlSam.kicad_pcb, ControlSam.kicad_sch]
2023-04-11 Some changes to Mikro
    [Control.kicad_sch]
2023-04-18 Updated sam-schematic
    Two Mikroe headers.
    [ControlSam.kicad_sch]
2023-05-13 Two Mikro
    [ControlSam.kicad_sch]
2023-05-18 Simplified a bit
    simplified
    [ControlSam.kicad_sch]
2023-05-19 Update ControlSam.kicad_sch
    Tidying
    [ControlSam.kicad_sch]
2023-05-20 Update ControlSam.kicad_sch
    Sync
    [ControlSam.kicad_sch]
2023-05-20 Footprint for vertical USB
    https://www.lcsc.com/product-detail/USB-Connectors_G-Switch-G-Switch-GT-USB-7038E_C2982477.html
2023-08-13 Create pico-notes
2023-09-04 Pico version
    [smartcar_control_2.0.kicad_pcb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]
